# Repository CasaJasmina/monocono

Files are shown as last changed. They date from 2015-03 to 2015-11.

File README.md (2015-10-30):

# monocono
Monocono is a kinetic artwork inspired by Strutturazioni cilindriche virtuali by Giovanni Anceschi (1963 -1966)

# BOM

| ingredient | Quantity | LINK|
| --- |:---:| :---:|
| Monocono Board | 1 | https://github.com/CasaJasmina/monocono/tree/master/pcb|
| Attiny 45 DIP | 1 | http://www.mouser.it/ProductDetail/Atmel/ATtiny45-20PU/?qs=sGAEpiMZZMtkfMPOFRTOlx1CkBXXGWZD|
| Dip 8 socket | 1 | http://www.mouser.it/Search/ProductDetail.aspx?R=DILB8P-223TLFvirtualkey64910000virtualkey649-DILB8P223TLF
| USB type B female | 1 | https://www.mouser.it/Search/ProductDetail.aspx?R=UE27-BC54-130virtualkey52350000virtualkey523-UE27-BC54-130| 
| 10kohm resistor | 1 | http://www.mouser.it/Search/ProductDetail.aspx?R=CFR25J10Kvirtualkey20420000virtualkey279-CFR25J10K
| 220ohm resistor | 1 |http://www.mouser.it/Search/ProductDetail.aspx?R=CCF07220RJKE36virtualkey61300000virtualkey71-CCF07220RJKE36
| 1kohm resistor | 1 | http://www.mouser.it/Search/ProductDetail.aspx?R=CCF501K00JKE36virtualkey61300000virtualkey71-CCF501K00JKE36
| diode | 1 | http://www.mouser.it/Search/ProductDetail.aspx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|
| led | 1 | http://www.mouser.it/Search/ProductDetail.aspx?R=LTL-4223virtualkey57820000virtualkey859-LTL-4223
| 2N7000 Mosfet | 1 | http://www.mouser.it/Search/ProductDetail.aspx?R=2N7000TAvirtualkey51210000virtualkey512-2N7000TA|
| 10uF capacitor | 1 | http://www.mouser.it/Search/ProductDetail.aspx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
| 0.1uF capacitor | 1 | http://www.mouser.it/Search/ProductDetail.aspx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|
| 100k potentiometer | 1 | http://www.mouser.it/ProductDetail/Alpha-Taiwan/RV24AF-10-15R1-A10K-3/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
| dc motor | 1 | http://www.robot-italy.com/it/hobby-motor-gear.html
| M3 screws + bolts | 9 | http://www.amazon.com/dp/B000NHXP66/ref=biss_dp_t_asn - http://www.amazon.com/100Pcs-Female-Thread-Fastener-Silver/dp/B00GYS1SXU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
| Wooden box | 1 | https://github.com/CasaJasmina/monocono/blob/master/construction/monocono_cube.dxf|
| 3d printed stick holder | 1 | https://github.com/CasaJasmina/monocono/blob/master/construction/stick_holder.stl|
| plastick sticks | 2 | |
| black tape | 1 | |

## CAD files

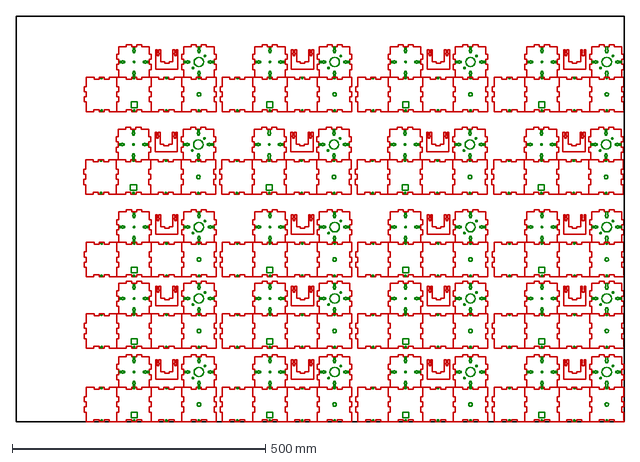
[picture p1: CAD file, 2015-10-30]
construction/20Case.dxf
1200.0 x 800.0 mm

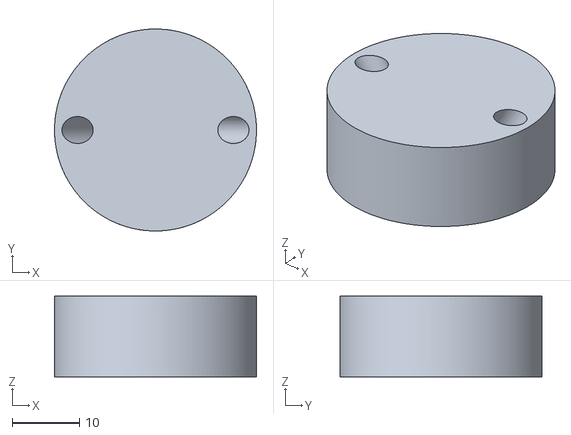
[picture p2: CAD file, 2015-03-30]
construction/stick_holder.stl
30.0 x 30.0 x 12.0

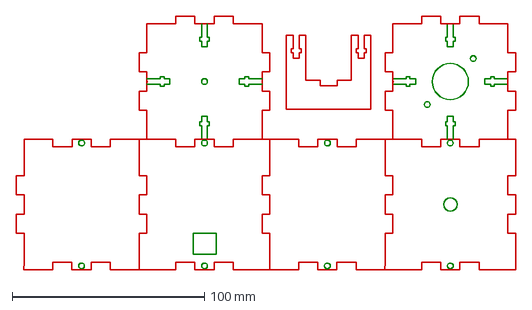
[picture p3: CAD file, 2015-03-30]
construction/monocono_cube.dxf
260.0 x 132.0 mm

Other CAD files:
construction/monocono.3dm
construction/monocono_cube.3dm

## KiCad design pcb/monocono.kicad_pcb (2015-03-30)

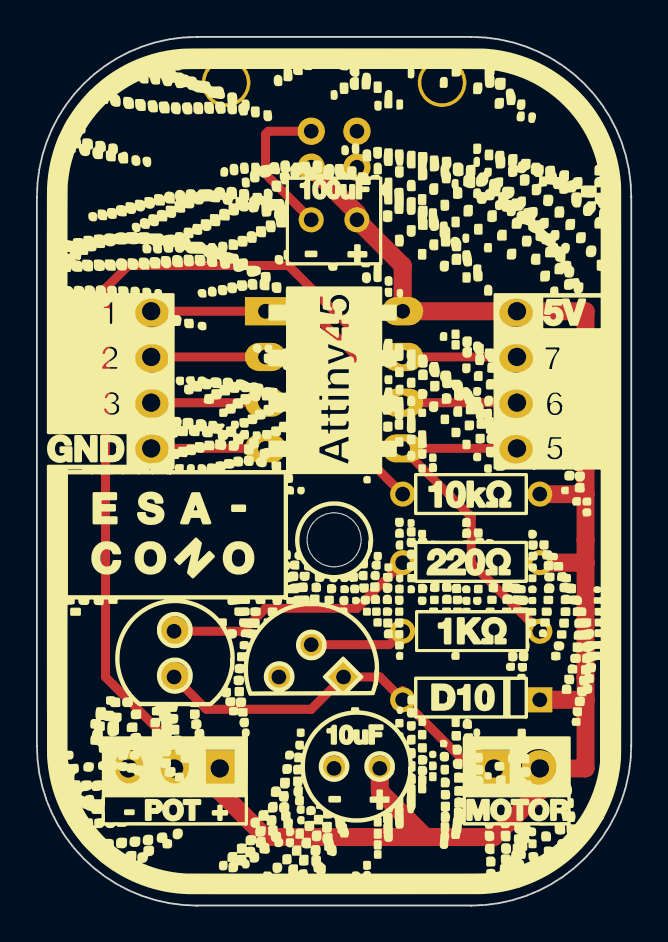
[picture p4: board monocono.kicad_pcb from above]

Board: 2 copper layers, 33.0 x 48.3 mm, 14 parts (0 on the bottom side), 11 nets.

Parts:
C1: 100nF; C1
C2: 10uF; C1
D1: LED; LED-5MM
D2: DIODE; D3
IC1: ATTINY45-P; DIP-8__300_ELL
J1: USB; USB_B
P1: P?; Socket_Strip_Straight_1x04
P2: CONN_01X04; Socket_Strip_Straight_1x04
P3: CONN_01X02; Socket_Strip_Straight_1x02
Q1: BS170; TO92
R1: 1k; R3
R2: 220; R3
R3: 10k; R3
RV1: 10k; Pin_Header_Straight_1x03

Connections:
+5V: C1.1, C2.1, D2.2, IC1.8, J1.1, P2.4, P3.2, R2.1, R3.1, RV1.1
GND: C1.2, C2.2, IC1.4, J1.4, P1.4, Q1.3, RV1.3
unnamed: D1.1, R2.2
unnamed: D1.2, D2.1, P3.1, Q1.1
unnamed: IC1.1, P1.1, R3.2
unnamed: IC1.2, P1.2
unnamed: IC1.3, P1.3
unnamed: IC1.5, P2.1, R1.2
unnamed: IC1.6, P2.2
unnamed: IC1.7, P2.3, RV1.2
unnamed: Q1.2, R1.1

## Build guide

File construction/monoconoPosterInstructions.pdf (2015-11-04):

GND321 | 5V765

MOTOR

D10

1KΩ

220KΩ

10KΩ

+

+

10uF

100uF

- POT +

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
C11 | C10
C12 | C13

USB port
Solder the four connectors and bend the hooks

Ceramic capacitor
It does not have a polarity
C01 | C01 C02

Microchip
Solder the 8 pins onto the base

Resistor 10k ohm
Orange-black-brown

Resistor 1k ohm
Red-black-brown

Red LED
One side of the LED is flat like the shape on the board

Screw
Use it to stack the board to the laser cut base

DC motor
Solder the red cable to the rounded connection (–) and the black on the square one (+)

Resistor 220 ohm
Brown-red-red

Diode D10
It has a polarity. Check the position of the white line

Potentiometer
It has three pins. The one on the left and the one in the center go into the rounded connection (–). The left one goes into the square connection (+)

After you finish soldering, start assembling the lasercut shell.
Push gently the bolts in the holes of each laser cut part and then use the screws to assemble them together.

Electrolitic capacitor
Solder the long leg to the positive connection and the short leg to the negative one

Transistor
It has a flat side like the shape on the board

Microchip
Stack it on the base, but only at the very end!
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
C03 | C01

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
Monocono is a do-it-yourself kinetic and programmed artwork. It is a USB powered electronic kit featuring digitally fabricated parts and a programmable board. A potentiometer controls the speed of a small motor that drives two rods and creates the effect of a virtual conic volume. Monocono is a derivative kinetic artwork inspired to Esacono,
a translation of the concept that generated the series Strutturazioni cilindriche virtuali by Giovanni Anceschi (1963–1966). The Esacono concept is described in issue no. 22 of the maga
zine il verri, but it was never produced due to the constraints of technology of the period. It is a cube suspended by one corner which has six motors embedded into each side.
The motors drive two rotating rods that draw six truncated cone shapes in space, creating virtual volumes. The speed varies from motor to motor, and as a consequence so does the

# MONOCONO

effect of the six shapes drawn in the air at the sides of the hanging cube. In 2015, Esacono has been realized within the project Re-programmed art, a research-action aiming at open sourcing and rediscovering kinetic and programmed art today.
Credits
The kit has been conceived and designed by Lorenzo Romagnoli, Federico Vanzati and Alessandro Gueli for Officine Arduino
www.arduino.cc
To make your own Monocono, visit www.github.com/casajasmina/monocono If you want to lean more about open source kinetic and programmed art visit www.reprogrammed-art.cc
Released under CC license BY SA 4.0 Graphic design
Leonardo Angelucci

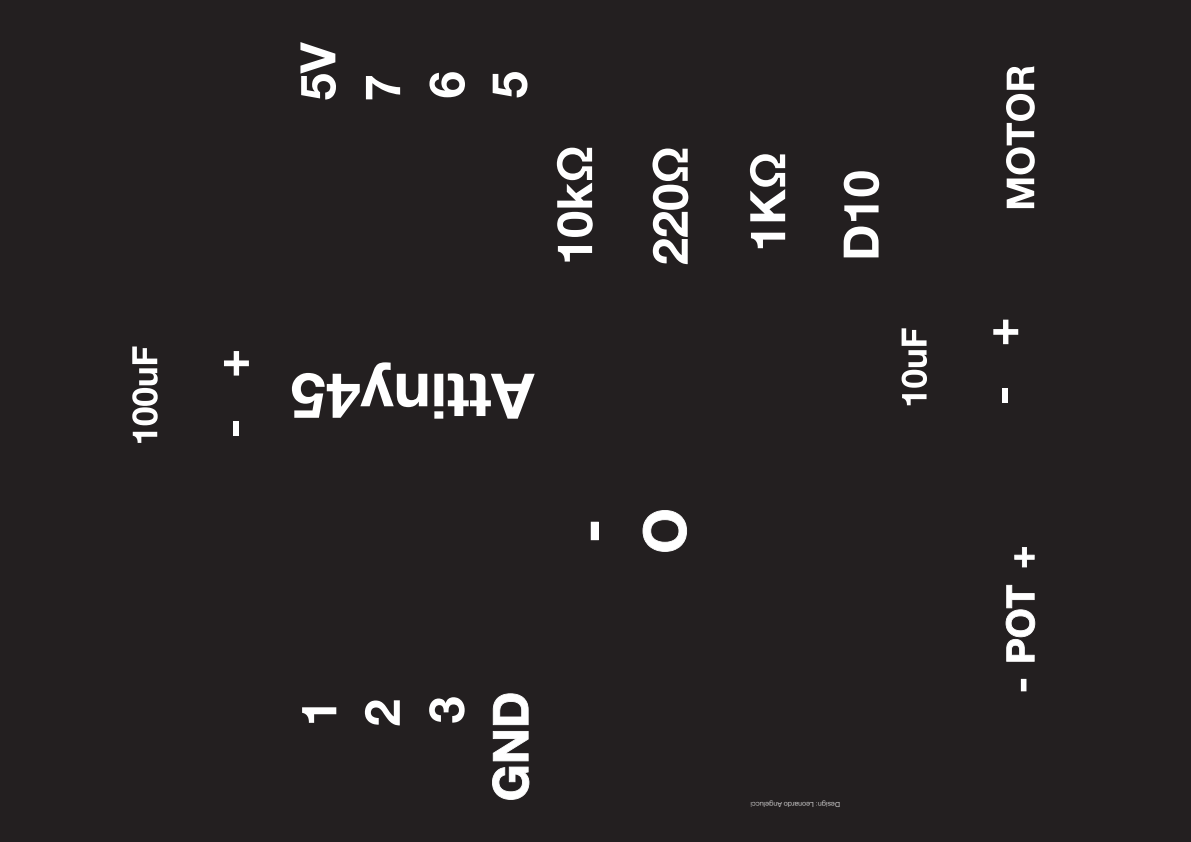
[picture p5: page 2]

Design: Leonardo Angelucci

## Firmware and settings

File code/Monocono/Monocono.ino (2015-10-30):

const int analogInPin = A1;  // Analog input pin that the potentiometer is attached to
const int analogOutPin = 0; // Analog output pin that the LED is attached to

int sensorValue = 0;        // value read from the pot
int outputValue = 0;        // value output to the PWM (analog out)

void setup() {
  pinMode(analogInPin, INPUT);
  pinMode(analogOutPin, OUTPUT);
 
}

void loop() {
  // read the analog in value:
  sensorValue = analogRead(analogInPin);
  // map it to the range of the analog out:
  outputValue = map(sensorValue,0,1023, 0, 255);
  // change the analog out value:
  analogWrite(analogOutPin, outputValue);
  delay(2);
}

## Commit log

2015-03-30 added pcb files
    [esacono-B_Cu.gbr, esacono-B_Mask.gbr, esacono-B_SilkS.gbr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]
2015-03-30 added construction files: laser+3dprint
    [monocono.3dm, monocono_cube.dxf, stick_holder.stl]
2015-10-29 added bom
2015-10-30 added code
    [20Case.dxf, monocono_cube.3dm]
